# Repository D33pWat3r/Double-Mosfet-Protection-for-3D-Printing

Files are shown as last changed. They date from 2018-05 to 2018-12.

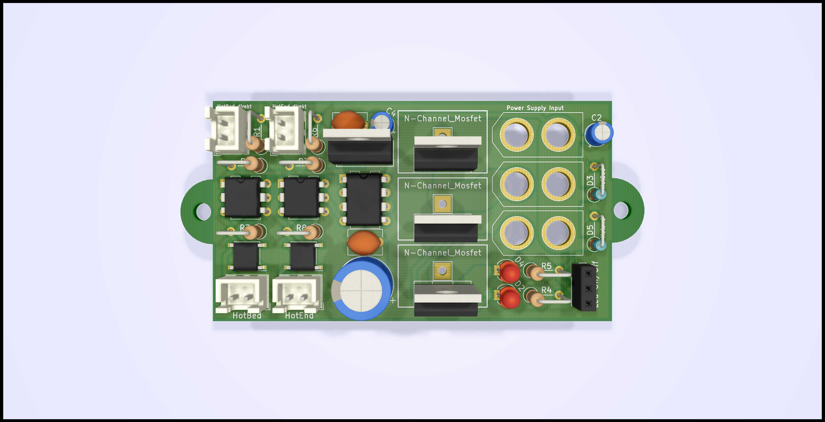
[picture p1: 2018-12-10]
KiCad Files/front.png

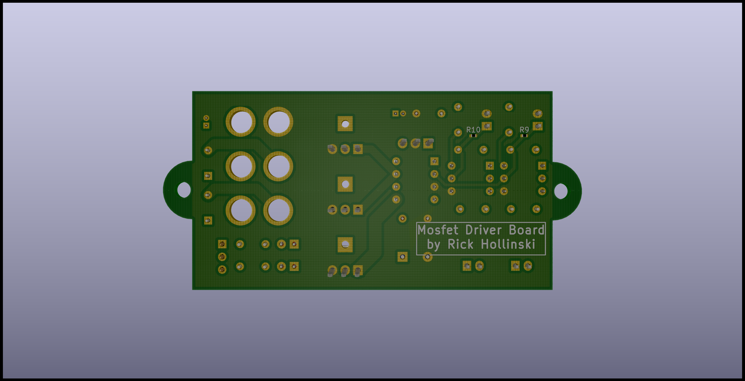
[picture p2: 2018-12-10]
KiCad Files/back.png

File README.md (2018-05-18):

# Double-Mosfet-Protection-for-3D-Printing

For my Anet A8 I will change to a 24V / 600W Power Supply to heating my hotbed and hotend faster.
The mainboard of a Anet A8 will not handle 24V and I must seperate the power to a extern circuit.

With a normal hotbed (1,3 Ohm) with a 24V system the current will rise drastically (ca. 18A).
Due to the high currents, the resistance of the transistors should be chosen as low as possible.

On Github you can find the circuit diagrams of the Anet A8 / A6 and typical mosfet protection boards from Aliexpress.
* [Anet 3D Board - Hardware Reverse Engineering Projekt on Github ](https://github.com/ralf-e/ANET-3D-Board-V1.0)

## Mainboard of Anet
[Mainboard](https://chinadrucker.de/wp-content/uploads/2017/07/072917_1833_ListederErs7.png)



On the normal mainboard of the Anet A8 there are IRLR7843PbF mosfets to manage the power of hotbed and hotend.
This onboard mosfet has a resistance of ~3mOhm and a thermalresistor of 1,05K/W. This mosfet can handle a lot of power. But if I change my System to 24V and more, than I must handle a current over 20A. The Thermalresistor of the onboard mosfet is not the best and the heatsink for the mosfet are not trustable.

* [Datasheet of IRLR7843PbF](https://www.infineon.com/dgdl/irlr7843pbf.pdf?fileId=5546d462533600a40153566de53526d8)

I will take the connectors for hotbed and hotend on the mainboard, which can switch my extern double mosfet board. I change the connectors of the mainbord to JST-XH connectors, because no high currents flow over it anymore.

## Extern Mosfet Protection Boards
[Example protection Board on Aliexpress](https://de.aliexpress.com/item/3D-Printer-Parts-Heated-Bed-Power-Module-Board-25A-MOSFET-For-Chitu-Motherboard/32814486198.html)



This boards has mosfets of the typ HA210N06 or YMP200N08Q which have a resistance of 3mOhm and a thermalresistance of 0,75. 

Instead, I take the mosfets of type IRF1404 because this Mosfets are cheap and have with a resistance of 4mOhm a litte bit more but a better thermalresistance.
Perhaps a take the better IRFB7430 Mosfet with some better values.
Furthermore get every power line (hotbed and hotend) 2 Mosfet. So I have some of redundancy and the half of resistance.

The main reason for a own and "better" extern mosfet board is the bad switching process by a voltage divider with two 10k resistors. This prozess needs time, where the RDs_on is chaning to high and low and produce heat. This is the reason for this ridiculous big heatsinks. Furthermore the mosfets have the best RDS_on by 10V and a voltage divider takes only the half of power voltage.

For easy plug, high-current XT60 Plugins are installed. This Connectors can handle 50A over a long time and have low connector resistance.
For the cables I take AWG 12-10 silicone cable with 3,3mm² - 5,2mm². The cable thickness is probably too much, but better too much than too low ;)

* [Datasheet of HA210N06](http://www.cecb2b.com/batchupload/inventoryother/zfa_ic_inventory/201495/zfa__332199_f13c9a0a038c37904c57614f101672ad.PDF)
* [Datasheet of YMP200N08Q](http://www.2150692.ru/files/ymp200n08q.pdf)
* [Datasheet of IRF1404](http://www.irf.com/product-info/datasheets/data/irf1404.pdf)
* [Datasheet of IRFB7430](https://github.com/D33pWat3r/Double-Mosfet-Protection-for-3D-Printing/blob/master/datasheets/datasheet_irfb7430pbf.pdf)

# References
- [Reference to https://3dprinterwiki.info/](https://3dprinterwiki.info/heatbed-terminal-burning-fix-with-mosfet-board/)

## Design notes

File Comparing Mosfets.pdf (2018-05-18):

Voltage Power 10 V 77 W 11 V 93 W | R_DS(on) R_th_JC 0,0026 1,05 | R_DS(on) R_th_JC 0,0035 0,45 | R_DS(on) 0,003
| Current Powerlost Thermalresistor 7,68 A 0,15 W 880 K/W 8,44 A 0,19 W 727 K/W | Current Power Thermalresistor 7,67 A 0,21 W 655 K/W 8,44 A 0,25 W 541 K/W | Current Power 7,67 A 0,18 W 8,44 A 0,21 W
12 V | 110 W | 9,21 A 0,22 W 611 K/W | 9,21 A 0,30 W 455 K/W | 9,21 A 0,25 W
13 V 130 W 14 V 150 W 15 V 173 W 16 V 196 W 17 V 222 W 18 V 249 W 19 V 277 W 20 V 307 W 21 V 338 W 22 V 371 W 23 V 406 W | | 9,98 A 0,26 W 520 K/W 10,75 A 0,30 W 448 K/W 11,52 A 0,34 W 391 K/W 12,28 A 0,39 W 343 K/W 13,05 A 0,44 W 304 K/W 13,82 A 0,50 W 271 K/W 14,59 A 0,55 W 243 K/W 15,35 A 0,61 W 219 K/W 16,12 A 0,68 W 199 K/W 16,89 A 0,74 W 181 K/W 17,66 A 0,81 W 165 K/W | 9,97 A 0,35 W 387 K/W 10,74 A 0,40 W 334 K/W 11,51 A 0,46 W 291 K/W 12,27 A 0,53 W 256 K/W 13,04 A 0,60 W 226 K/W 13,81 A 0,67 W 202 K/W 14,58 A 0,74 W 181 K/W 15,34 A 0,82 W 163 K/W 16,11 A 0,91 W 148 K/W 16,88 A 1,00 W 135 K/W 17,64 A 1,09 W 123 K/W | 9,98 A 0,30 W 10,74 A 0,35 W 11,51 A 0,40 W 12,28 A 0,45 W 13,05 A 0,51 W 13,81 A 0,57 W 14,58 A 0,64 W 15,35 A 0,71 W 16,12 A 0,78 W 16,88 A 0,86 W 17,65 A 0,93 W
24 V | 442 W | 18,42 A 0,88 W 152 K/W | 18,41 A 1,19 W 113 K/W | 18,42 A 1,02 W
25 V 479 W 26 V 519 W 27 V 559 W 28 V 601 W 29 V 645 W 30 V 690 W | | 19,19 A 0,96 W 140 K/W 19,96 A 1,04 W 129 K/W 20,73 A 1,12 W 120 K/W 21,50 A 1,20 W 111 K/W 22,26 A 1,29 W 104 K/W 23,03 A 1,38 W 97 K/W | 19,18 A 1,29 W 104 K/W 19,95 A 1,39 W 96 K/W 20,71 A 1,50 W 89 K/W 21,48 A 1,61 W 83 K/W 22,25 A 1,73 W 77 K/W 23,01 A 1,85 W 72 K/W | 19,19 A 1,10 W 19,95 A 1,19 W 20,72 A 1,29 W 21,49 A 1,39 W 22,26 A 1,49 W 23,02 A 1,59 W

# Hotbed

Resistor | 1,3

# Mosfets

IRLR7843PbF | IRF1404 | YMP200N08Q

31 V 737 W 32 V 786 W 33 V 835 W 34 V 887 W 35 V 940 W | 23,80 A 1,47 W 91 K/W 24,57 A 1,57 W 85 K/W 25,33 A 1,67 W 80 K/W 26,10 A 1,77 W 75 K/W 26,87 A 1,88 W 71 K/W | 23,78 A 1,98 W 68 K/W 24,55 A 2,11 W 64 K/W 25,32 A 2,24 W 60 K/W 26,08 A 2,38 W 56 K/W 26,85 A 2,52 W 53 K/W | 23,79 A 1,70 W 24,56 A 1,81 W 25,33 A 1,92 W 26,09 A 2,04 W 26,86 A 2,16 W
36 V | 994 W | 27,64 A 1,99 W 67 K/W | 27,62 A 2,67 W 50 K/W | 27,63 A 2,29 W
Voltage Power 10 V 36 W 11 V 43 W | R_DS(on) R_th_JC 0,0026 1,05 | R_DS(on) R_th_JC 0,0035 0,45 | R_DS(on) 0,003
| Current Powerlost Thermalresistor 3,57 A 0,03 W 4077 K/W 3,92 A 0,04 W 3369 K/W | Current Power Thermalresistor 3,57 A 0,04 W 3031 K/W 3,92 A 0,05 W 2505 K/W | Current Power 3,57 A 0,04 W 3,92 A 0,05 W
12 V | 51 W | 4,28 A 0,05 W 2831 K/W | 4,28 A 0,06 W 2105 K/W | 4,28 A 0,05 W
13 V 60 W 14 V 70 W 15 V 80 W 16 V 91 W 17 V 103 W 18 V 116 W 19 V 129 W 20 V 143 W 21 V 157 W 22 V 173 W 23 V 189 W | | 4,64 A 0,06 W 2412 K/W 5,00 A 0,06 W 2080 K/W 5,35 A 0,07 W 1812 K/W 5,71 A 0,08 W 1592 K/W 6,07 A 0,10 W 1410 K/W 6,42 A 0,11 W 1258 K/W 6,78 A 0,12 W 1129 K/W 7,14 A 0,13 W 1019 K/W 7,49 A 0,15 W 924 K/W 7,85 A 0,16 W 842 K/W 8,21 A 0,18 W 770 K/W | 4,64 A 0,08 W 1793 K/W 4,99 A 0,09 W 1546 K/W 5,35 A 0,10 W 1347 K/W 5,71 A 0,11 W 1184 K/W 6,06 A 0,13 W 1049 K/W 6,42 A 0,14 W 935 K/W 6,78 A 0,16 W 839 K/W 7,13 A 0,18 W 757 K/W 7,49 A 0,20 W 687 K/W 7,85 A 0,22 W 626 K/W 8,20 A 0,24 W 573 K/W | 4,64 A 0,06 W 4,99 A 0,07 W 5,35 A 0,09 W 5,71 A 0,10 W 6,06 A 0,11 W 6,42 A 0,12 W 6,78 A 0,14 W 7,14 A 0,15 W 7,49 A 0,17 W 7,85 A 0,18 W 8,21 A 0,20 W

# Resistor

IRLR7843PbF | IRF1404 | YMP200N08Q

# Hotend

2,8

# Mosfets

24 V | 205 W | 8,56 A 0,19 W 707 K/W | 8,56 A 0,26 W 526 K/W | 8,56 A 0,22 W
25 V 223 W 26 V 241 W 27 V 260 W 28 V 280 W 29 V 300 W 30 V 321 W 31 V 343 W 32 V 365 W 33 V 388 W 34 V 412 W 35 V 437 W | | 8,92 A 0,21 W 651 K/W 9,28 A 0,22 W 602 K/W 9,63 A 0,24 W 558 K/W 9,99 A 0,26 W 519 K/W 10,35 A 0,28 W 484 K/W 10,70 A 0,30 W 452 K/W 11,06 A 0,32 W 423 K/W 11,42 A 0,34 W 397 K/W 11,77 A 0,36 W 373 K/W 12,13 A 0,38 W 352 K/W 12,49 A 0,41 W 332 K/W | 8,92 A 0,28 W 485 K/W 9,27 A 0,30 W 448 K/W 9,63 A 0,32 W 415 K/W 9,99 A 0,35 W 386 K/W 10,34 A 0,37 W 360 K/W 10,70 A 0,40 W 336 K/W 11,06 A 0,43 W 315 K/W 11,41 A 0,46 W 296 K/W 11,77 A 0,48 W 278 K/W 12,13 A 0,51 W 262 K/W 12,48 A 0,55 W 247 K/W | 8,92 A 0,24 W 9,28 A 0,26 W 9,63 A 0,28 W 9,99 A 0,30 W 10,35 A 0,32 W 10,70 A 0,34 W 11,06 A 0,37 W 11,42 A 0,39 W 11,77 A 0,42 W 12,13 A 0,44 W 12,49 A 0,47 W
36 V | 462 W | 12,85 A 0,43 W 314 K/W | 12,84 A 0,58 W 233 K/W | 12,84 A 0,49 W

R_th_JC 0,75 | IRFB7430 R_DS(on) R_th_JC 0,001 0,4
Thermalresistor 763 K/W 631 K/W | Current Power Thermalresistor 7,69 A 0,06 W 2285 K/W 8,46 A 0,07 W 1888 K/W
530 K/W | 9,22 A 0,09 W 1586 K/W
451 K/W 389 K/W 339 K/W 298 K/W 264 K/W 235 K/W 211 K/W 190 K/W 172 K/W 157 K/W 144 K/W | 9,99 A 0,10 W 1352 K/W 10,76 A 0,12 W 1165 K/W 11,53 A 0,13 W 1015 K/W 12,30 A 0,15 W 892 K/W 13,07 A 0,17 W 790 K/W 13,84 A 0,19 W 705 K/W 14,60 A 0,21 W 633 K/W 15,37 A 0,24 W 571 K/W 16,14 A 0,26 W 518 K/W 16,91 A 0,29 W 472 K/W 17,68 A 0,31 W 431 K/W
132 K/W | 18,45 A 0,34 W 396 K/W
121 K/W 112 K/W 104 K/W 97 K/W 90 K/W 84 K/W | 19,22 A 0,37 W 365 K/W 19,98 A 0,40 W 338 K/W 20,75 A 0,43 W 313 K/W 21,52 A 0,46 W 291 K/W 22,29 A 0,50 W 271 K/W 23,06 A 0,53 W 253 K/W

79 K/W 74 K/W 69 K/W 65 K/W 62 K/W | 23,83 A 0,57 W 237 K/W 24,60 A 0,60 W 223 K/W 25,37 A 0,64 W 209 K/W 26,13 A 0,68 W 197 K/W 26,90 A 0,72 W 186 K/W
58 K/W | 27,67 A 0,77 W 176 K/W
R_th_JC 0,75 | IRFB7430 R_DS(on) R_th_JC 0,001 0,4
Thermalresistor 3535 K/W 2921 K/W | Current Power Thermalresistor 3,57 A 0,01 W 10591 K/W 3,93 A 0,02 W 8753 K/W
2455 K/W | 4,28 A 0,02 W 7355 K/W
2091 K/W 1803 K/W 1571 K/W 1380 K/W 1223 K/W 1090 K/W 979 K/W 883 K/W 801 K/W 730 K/W 668 K/W | 4,64 A 0,02 W 6267 K/W 5,00 A 0,02 W 5403 K/W 5,36 A 0,03 W 4707 K/W 5,71 A 0,03 W 4137 K/W 6,07 A 0,04 W 3664 K/W 6,43 A 0,04 W 3269 K/W 6,78 A 0,05 W 2934 K/W 7,14 A 0,05 W 2647 K/W 7,50 A 0,06 W 2401 K/W 7,85 A 0,06 W 2188 K/W 8,21 A 0,07 W 2002 K/W

2,8 ohm for 12V version
12 ohm for 24 V version

613 K/W | 8,57 A 0,07 W 1838 K/W
565 K/W 522 K/W 484 K/W 450 K/W 420 K/W 392 K/W 367 K/W 345 K/W 324 K/W 305 K/W 288 K/W | 8,93 A 0,08 W 1694 K/W 9,28 A 0,09 W 1566 K/W 9,64 A 0,09 W 1452 K/W 10,00 A 0,10 W 1351 K/W 10,35 A 0,11 W 1259 K/W 10,71 A 0,11 W 1176 K/W 11,07 A 0,12 W 1102 K/W 11,42 A 0,13 W 1034 K/W 11,78 A 0,14 W 972 K/W 12,14 A 0,15 W 916 K/W 12,50 A 0,16 W 864 K/W
272 K/W | 12,85 A 0,17 W 817 K/W

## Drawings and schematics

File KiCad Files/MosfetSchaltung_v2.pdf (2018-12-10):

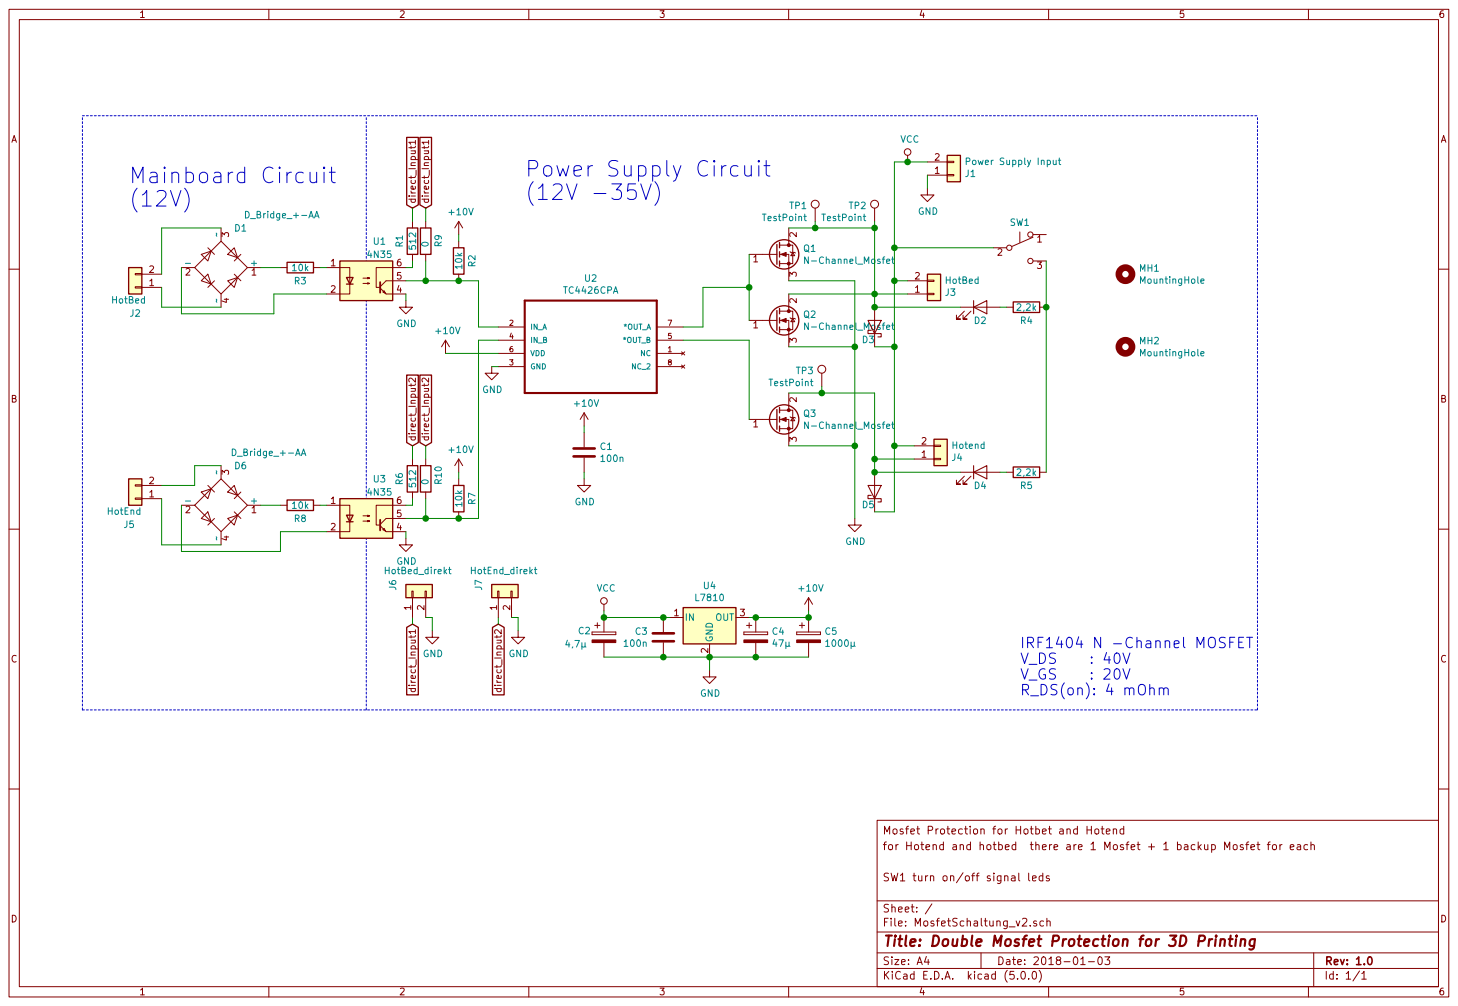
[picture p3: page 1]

for Hotend and hotbed there are 1 Mosfet + 1 backup Mosfet for each Mosfet Protection for Hotbet and Hotend Mainboard Circuit

File: MosfetSchaltung_v2.sch Sheet: / SW1 turn on/off signal leds

Id: 1/1 Title: Double Mosfet Protection for 3D Printing

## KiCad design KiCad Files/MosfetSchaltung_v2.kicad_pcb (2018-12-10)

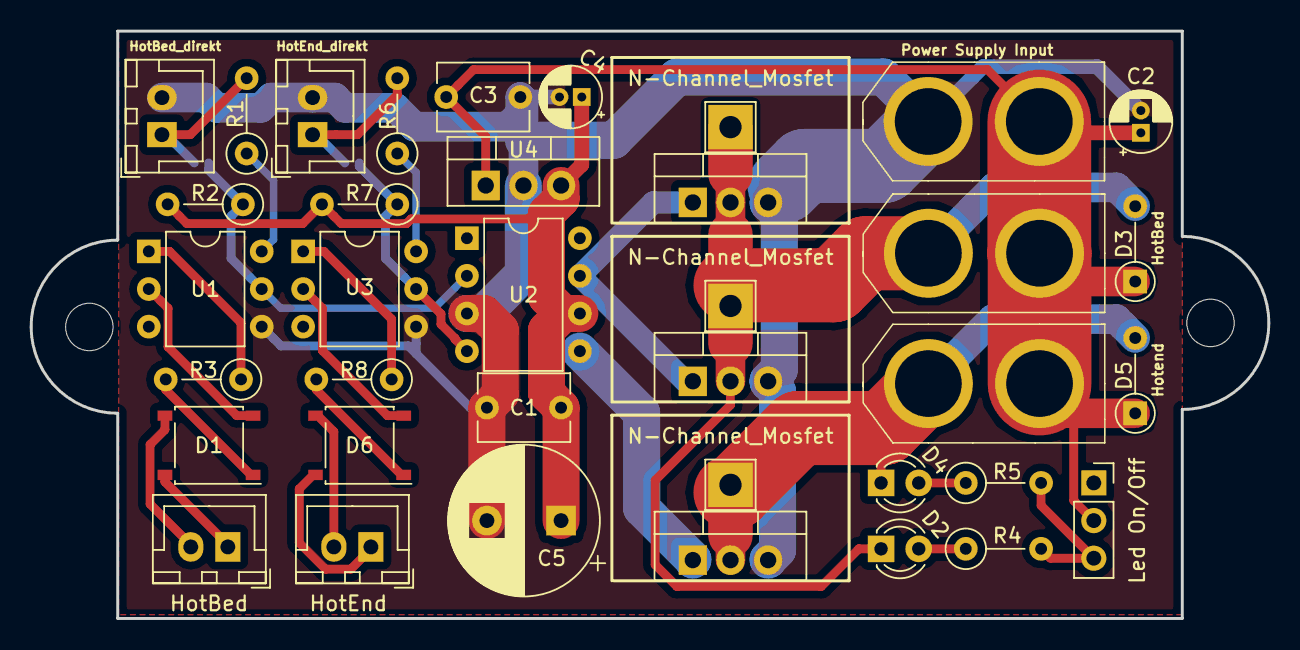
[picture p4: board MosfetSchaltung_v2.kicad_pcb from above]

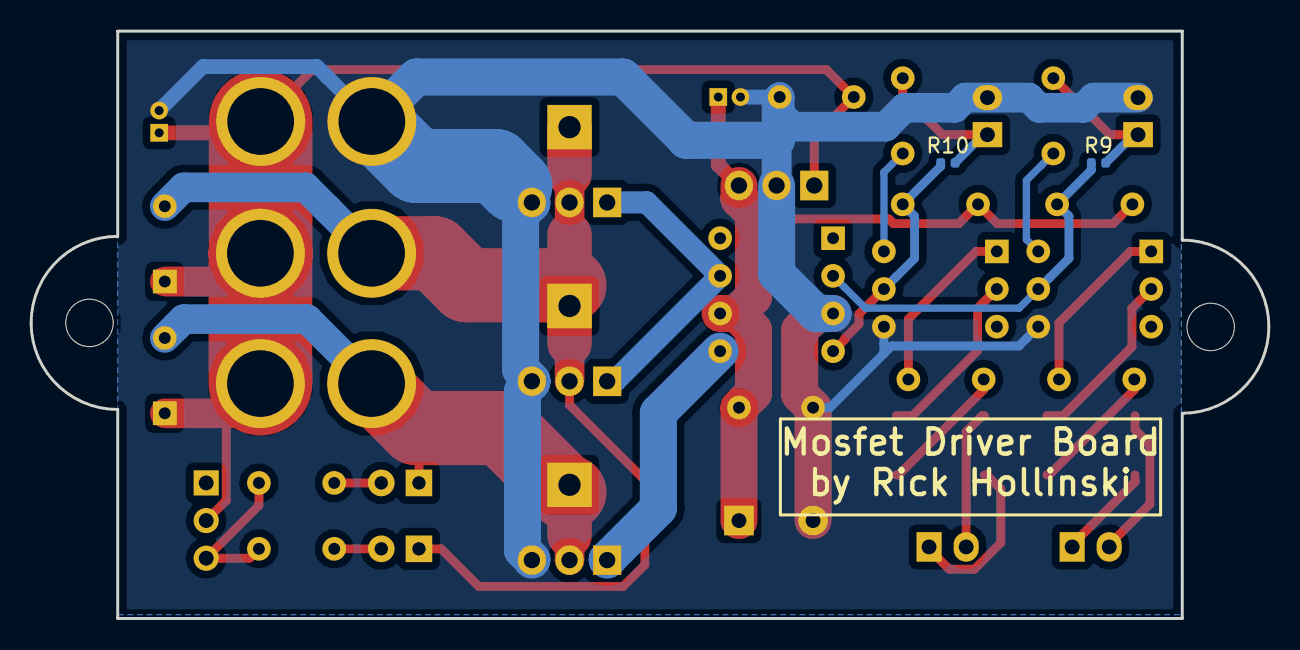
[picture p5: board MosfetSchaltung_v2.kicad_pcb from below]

Board: 2 copper layers, 83.5 x 39.6 mm, 41 parts (4 on the bottom side), 26 nets.

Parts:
C1, C3: 100n; C_Disc_D6.0mm_W4.4mm_P5.00mm
C2: 4,7µ; CP_Radial_D4.0mm_P1.50mm
C4: 47µ; CP_Radial_D4.0mm_P1.50mm
C5: 1000µ; CP_Radial_D10.0mm_P5.00mm
D1, D6: D_Bridge_+-AA; Diode_Bridge_Diotec_ABS
D2, D4: LED; LED_D3.0mm
D3, D5: D_Schottky; D_DO-35_SOD27_P5.08mm_Vertical_AnodeUp
J1: Power Supply Input; XT60
J2: HotBed; JST_XH_B02B-XH-A_1x02_P2.50mm_Vertical
J3: HotBed; XT60
J4: Hotend; XT60
J5: HotEnd; JST_XH_B02B-XH-A_1x02_P2.50mm_Vertical
J6: HotBed_direkt; JST_XH_B02B-XH-A_1x02_P2.50mm_Vertical
J7: HotEnd_direkt; JST_XH_B02B-XH-A_1x02_P2.50mm_Vertical
MH1, MH2: MountingHole; MountingHole_3.2mm_M3
Q1, Q2, Q3: N-Channel_Mosfet; TO-220-3_Vertical
R1, R6: 512; R_Axial_DIN0207_L6.3mm_D2.5mm_P5.08mm_Vertical
R2, R3, R7, R8: 10k; R_Axial_DIN0207_L6.3mm_D2.5mm_P5.08mm_Vertical
R4, R5: 2,2k; R_Axial_DIN0207_L6.3mm_D2.5mm_P5.08mm_Vertical
R9, R10: 0; R_0402_1005Metric
SW1: Led On/Off; PinSocket_1x03_P2.54mm_Vertical
TP1, TP2, TP3: TestPoint; TestPoint_THTPad_3.0x3.0mm_Drill1.5mm
U1, U3: 4N35; DIP-6_W7.62mm
U2: TC4426CPA; DIP-8_W7.62mm
U4: L7810; TO-220-3_Vertical

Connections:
+10V: C1.1, C4.1, C5.1, R2.2, R7.2, U2.6, U4.3
GND: C1.2, C2.2, C3.2, C4.2, C5.2, J1.1, J6.2, J7.2, Q1.3, Q2.3, Q3.3, U1.4, U2.3, U3.4, U4.2
unnamed: D1.1, R3.2
unnamed: D1.2, U1.2
unnamed: D1.3, J2.2
unnamed: D1.4, J2.1
unnamed: D2.1, D3.2, J3.1, Q1.2, Q2.2, TP1.1, TP2.1
unnamed: D2.2, R4.1
unnamed: D4.1, D5.2, J4.1, Q3.2, TP3.1
unnamed: D4.2, R5.1
unnamed: D6.1, R8.2
unnamed: D6.2, U3.2
unnamed: D6.3, J5.2
unnamed: D6.4, J5.1
unnamed: Q1.1, Q2.1, U2.7
unnamed: Q3.1, U2.5
unnamed: R1.1, U1.6
unnamed: R2.1, R9.1, U1.5, U2.2
unnamed: R3.1, U1.1
unnamed: R4.2, R5.2, SW1.3
unnamed: R6.1, U3.6
unnamed: R8.1, U3.1
unnamed: R7.1, R10.1, U2.4, U3.5
VCC: C2.1, C3.1, D3.1, D5.1, J1.2, J3.2, J4.2, SW1.2, U4.1
direct_Input1: J6.1, R1.2, R9.2
direct_Input2: J7.1, R6.2, R10.2

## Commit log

2018-01-03 first Version of my Protection Board
    [MosfetSchaltung.sch]
2018-01-04 Calculation of Powerloss and heatings
    [Comparing Mosfets.xlsx]
2018-01-04 Calculation of Powerloss and heatings as pdf
2018-01-04 Datasheets for Mosfets
2018-01-04 XT60 Lib for Kicad
2018-01-04 corrected a mistake with the LED circuit
    [MosfetSchaltung.kicad_pcb]
2018-01-04 mark the 12V row
    [Comparing Mosfets.xlsx]
2018-01-04 delet pcb File
    [MosfetSchaltung.kicad_pcb]
2018-01-05 mark the 12V line
    [Comparing Mosfets.xlsx]
2018-02-02 change Gate Voltage to under 15V
    [MosfetSchaltung.sch]
2018-02-10 new design for 10-35V power supplies
    [MosfetSchaltung_v1.1.sch]
2018-03-30 first version with a volatge divider
    [MosfetSchaltung.sch]
2018-03-30 version with transistors for mosfet bank
    [MosfetSchaltung_v1.1.sch]
2018-03-30 version with an inverted dual MosfetDriver
    [MosfetSchaltung_v1.1.sch]
2018-03-30 new folder struckture
    [MosfetSchaltung.sch, MosfetSchaltung_v1.1.sch]
2018-05-18 add 2 flyback diodes; move status leds to output; add direct input connectors
    [Comparing Mosfets.xlsx, MosfetSchaltung_v1.1.sch, MosfetSchaltung_v2.sch]
2018-05-18 expand table to 36V and add a new Mosfet type
    [Comparing Mosfets.xlsx]
2018-05-18 change some values
    [Comparing Mosfets.xlsx]
2018-12-10 Gerber Files
    [MosfetSchaltung_v2-B.Cu.gbr, MosfetSchaltung_v2-B.Mask.gbr, MosfetSchaltung_v2-B.Paste.gbr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]
2018-12-10 KiCad Cicuits Files
    [MosfetSchaltung_v2.kicad_pcb, MosfetSchaltung_v2.sch]
2018-12-10 pictures of the circuit board
2018-12-11 clear files
    [Comparing Mosfets.xlsx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]
